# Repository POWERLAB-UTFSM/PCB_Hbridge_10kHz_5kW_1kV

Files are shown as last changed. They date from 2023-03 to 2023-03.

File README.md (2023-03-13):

# Proyecto PCB Hbridge

## Descripción

Repositorio con archivos necesarios para visualizar el esquematico y PCB del circuito Hbridge

## Requisitos

### Software

* KiCad, para diseño de esquemático y conversión a placa de circuito impreso
* Git, para control de versiones y manejo de repositorios.

## Contenido de carpetas:

* [PCB_Hbridge](PCB_Hbridge): Carpeta con archivos relacionados al esquematico y 
    * [BOM](PCB_Hbridge/BOM): Carpeta con lista detallada de todos los componentes electrónicos necesarios para construir un circuito impreso (PCB) obtenida directamente desde el software.
    * [GERBER](PCB_Hbridge/GERBER): Carpeta con archivos necesarios para la fabricación de la PCB.

* [BOM_v1](BOM_v1): Lista detallada con los componentes y su precio, dando un estimado del presupuesto necesario para su fabricación.

* [Documento_de_diseno](Documento_de_diseno): Documento que respalda el diseño y desarrollo del circuito implementado en la PCB

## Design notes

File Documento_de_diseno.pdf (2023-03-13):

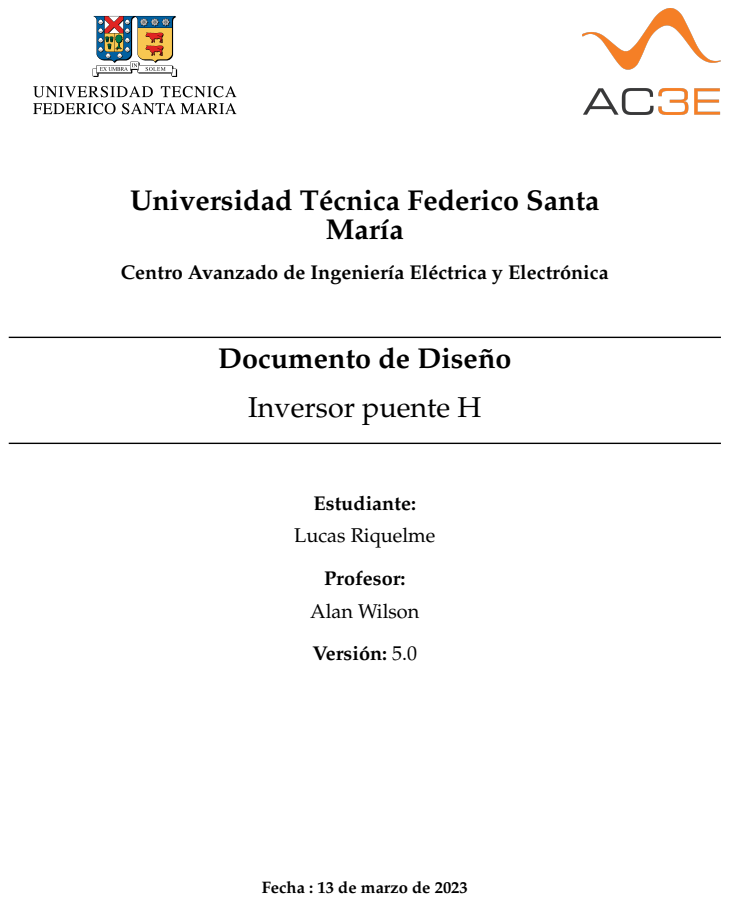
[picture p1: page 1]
María; Estudiante:; Lucas Riquelme; Profesor:; Alan Wilson; Versión: 5.0

Universidad Técnica Federico Santa

Centro Avanzado de Ingeniería Eléctrica y Electrónica

Documento de Dise ño
Inversor puente H

Fecha : 13 de marzo de 2023

## Prefacio

Alcance del
documento

Establece los requisitos funcionales que debe cumplir el diseno del Inversor ˜ Puente H. Describe los siguientes aspectos del sistema: requisitos funciona-
| les, arquitectura del sistema a disenar, caracter ˜ | ísticas funcionales de cada
componente, descripcion de cada m ´ | odulo, incluyendo sus casos de prueba. ´
Autor | Lucas Riquelme
Lectores | Este documento esta dirigido principalmente al supervisor de pr ´ | actica ´

## Historia del documento

Versión | Fecha | Descripción del cambio | Autor
1.0 | 05/01/2023 | Primer documento LATEX | Lucas Riquelme
2.0 | 17/01/2023 | Se agregan secciones principales | Lucas Riquelme
3.0 | 30/01/2023 | Se agrega el desarrollo del modulo in- ´ versor y filtro | Lucas Riquelme
4.0 | 08/02/2023 | Se agrega el desarrollo del modulo ´ circuito de medicion´ | Lucas Riquelme
5.0 | 27/02/2023 | Se complementa el desarrollo del cir-cuito de medicion y se agrega simula- ´ cion con rectificador en la secci ´ on de ´ filtro de salida | Lucas Riquelme
Documento de disenõ | 1

## Índice

1. Descripción y requisitos del sistema | 3
1.1. Proposito | ´ | 3
1.2. Requisitos funcionales | | 3
1.3. Alcances | | 3
2. Arquitectura del sistema | 4
2.1. Diagrama de bloques | | 4
2.2. Enumeracion de m ´ | odulos | ´ | 4
3. Descripción de los módulos | 5
3.1. Modulo Inversor monof ´ | asico | ´ | 5
3.1.1. Definicion | ´ | 5
3.1.2. Diagrama del modulo | ´ | 5
3.1.3. Diseno del m ˜ | odulo | ´ | 5
3.1.4. Estrategia de prueba del modulo | ´ | 8
3.2. Modulo Filtro paso bajos | ´ | 9
3.2.1. Definicion | ´ | 9
3.2.2. Diagrama del modulo | ´ | 9
3.2.3. Diseno del m ˜ | odulo | ´ | 9
3.2.4. Estrategia de prueba del modulo | ´ | 13
3.3. Modulo Circuito de medici ´ | on | ´ | 14
3.3.1. Definicion | ´ | 14
3.3.2. Diagrama del modulo | ´ | 14
3.3.3. Diseno del m ˜ | odulo | ´ | 14
3.3.4. Estrategia de prueba del modulo | ´ | 17
3.4. Lista de componentes (BOM) | 18

## Índice de figuras

1. | Diagrama de bloques del sistema | | 4
2. | Diagrama de circuito del modulo Inversor monof ´ | asico | ´ | 5
3. | Esquematico del inversor puente H y modulaci ´ | on PWM unipolar | ´ | 6
4. | Resultados obtenidos en el modulo inversor monof ´ | asico | ´ | 7
5. | Filtro LC | | 9
6. | Esquematico del inversor puente H y filtro LC | ´ | 10
7. | Resultados obtenidos en el modulo filtro de salida | ´ | 11
8. | Esquematico del inversor m ´ | as filtro, considerando rectificador | ´ | 12
9. Resultados obtenidos utilizando el rectificador de entrada | 12
10. Diagrama de bloques del modulo circuito de medici ´ | on | ´ | 14
11. Circuito de sensor de voltaje | 15
12. Sensor de corriente integrado MLX91221 | 15
13. Convertidor DC/DC PDSE2-S24-S5-M | 16

## Índice de cuadros

1. | Modulos del sistema | ´ | 4
2. | Parametros base del inversor puente H a modelar | ´ | 7

## 1. Descripción y requisitos del sistema

Esta seccion explica el prop ´ | osito y funcionamiento general del sistema a dise ´ | nar, junto con ˜
describir los requisitos funcionales y alcances del sistema.

### 1.1. Propósito

El sistema corresponde a un convertidor DC/AC, el cual debe ser capaz de convertir un voltaje
continuo a una tension alterna de alta frecuencia. Adem ´ | as, de entregar se ´ | nales acondicionadas ˜
para observar las mediciones en la entrada y salida del sistema.

### 1.2. Requisitos funcionales

Los requisitos funcionales definen el comportamiento del sistema. En otras palabras, estos requisitos mínimos describen que es lo que debe hacer el sistema.

RF1 La tension continua de entrada de 1kV debe ser convertida en un voltaje conmutado con ´ frecuencia fundamental de 10kHz, el cual debe ser filtrado para obtener un voltaje alterno sin armonicos de alta frecuencia. ´

RF2 El sistema debe entregar una potencia de hasta 5kW.

RF3 El sistema es capaz de medir voltajes DC y AC de hasta 1kV.

RF4 Las senales an ˜ | alogas de las mediciones generadas por el circuito est ´ | an adaptadas para ran- ´
gos de ±5V para ser visualizadas en un osciloscopio.

### 1.3. Alcances

La entrada del sistema corresponde a un DC-link de 1kV obtenido a partir de un modulo ´ rectificador.

La salida del sistema debe estar conectada a un transformador, por tanto el voltaje alterno a la salida del sistema debe tener valor medio cero.

## 2. Arquitectura del sistema

Aquí se presenta la arquitectura que se empleara para desarrollar el Inversor puente H. ´

### 2.1. Diagrama de bloques

La siguiente figura muestra los modulos internos y externos del sistema, y sus principales ´ interacciones.

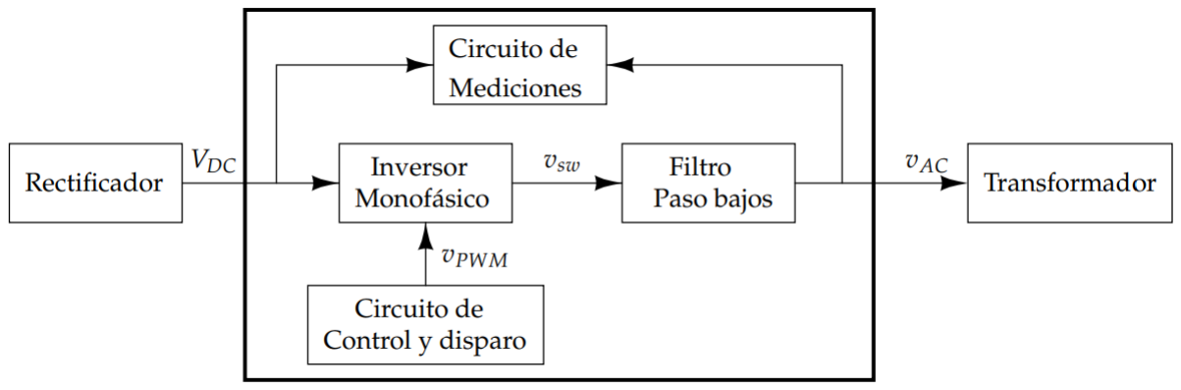
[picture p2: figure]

Figura 1: Diagrama de bloques del sistema

### 2.2. Enumeración de módulos

La Tabla 1 muestra los bloques de la Figura 1. Por cada modulo se entrega un breve p ´ | arrafo ´
descriptivo de su proposito. ´
Modulo ´ | Proposito ´
Inversor monofasico ´ | Convertir el voltaje continuo de entrada en una tension alterna ´
Filtro paso bajos | Filtrar los armonicos de alta frecuencia de una se ´ nal alterna ˜
Circuito de medicio-nes | Adapta los voltajes de entrada y salida
Circuito de control y disparo | Genera los pulsos de disparo que controlan al inversor

Cuadro 1: Modulos del sistema. ´

## 3. Descripción de los módulos

### 3.1. Módulo Inversor monofásico

### 3.1.1. Definición

Propósito: Convertir un voltaje dc de 1kV a una tension alterna de frecuencia 10kHz ´

### 3.1.2. Diagrama del módulo

La figura 2 muestra el diagrama del modulo Inversor monof ´ | asico. ´

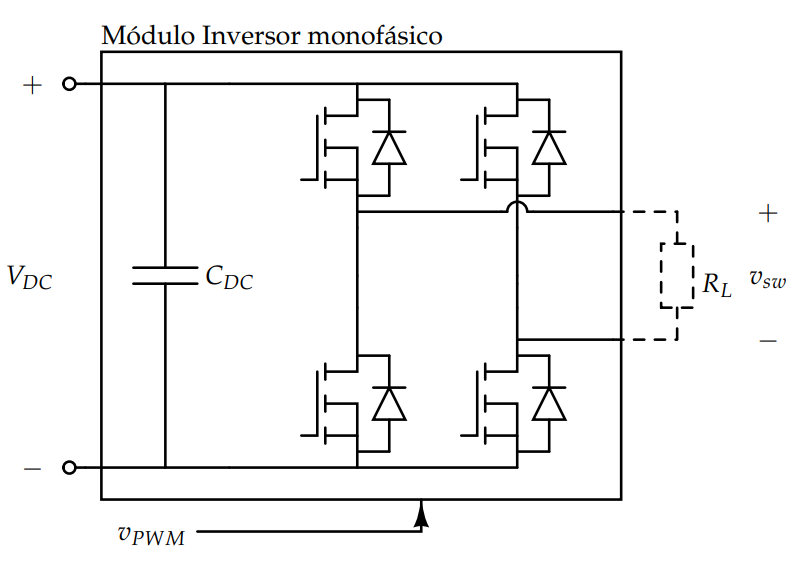
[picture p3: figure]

Figura 2: Diagrama de circuito del modulo Inversor monof ´ | asico. ´

### 3.1.3. Dise ño del módulo

Lo primero a considerar es el tipo de modulacion a utilizar, dado a que se necesita generar un ´ voltaje alterno con valor medio cero, se utiliza la modulacion PWM unipolar para generar una ´
tension a la salida de tres niveles. Hay que considerar que, al utilizar este tipo de modulaci ´ | on´
se obtendra una duplicaci ´ | on aparente de la frecuencia de conmutaci ´ | on a la salida, con lo que se ´
consigue alejar los armonicos de ´ | mf a 2mf ± 1.
Por otro lado, se escoge un índice de modulacion par ( ´ | mf = 10) dado a que permite eliminar los
armonicos pares que se generen, con este valor y considerando que la frecuencia de la fundamental ´ es f1 = 10kHz, es posible obtener el valor de la frecuencia de la portadora a utilizar,

fc = mf

f1 = 100kHz | (1)

Por otro lado, se sabe que el circuito debe entregar una potencia de hasta Po = 5kW a una tension´ Vdc = 1kV, es decir, la carga conectada debe ser una resistencia de,

RL =

(VDC)

2
P
= 200Ω | (2)

y por tanto, la corriente en la carga y en el semiconductor es,

IL =

VDC
RL
= 5A | (3)

Para el semiconductor, se utiliza el MOSFET de carburo de silicio dado a que generalmente operan a altas frecuencias y velocidad de conmutacion, y soportan una mayor temperatura de ´ juntura. Por otro lado, hay que tener en cuenta que estos deben ser capaces de operar a una frecuencia de 100kHz, soportar un voltaje de 1kV y una corriente de IL = 5A. Dado a que se debe tener un margen de seguridad en caso de algun peak de corriente o voltaje, al momento de escoger ´ un MOSFET se establecen los siguientes criterios,

VDSS ≥ 1,2 · VDC = 1200V | (4)
ID ≥ 2 · IL = 10A | (5)
Finalmente, para el diseno del condensador del DC-link, se considerar ˜ | a un criterio basado en ´
el rizado del voltaje DC, cuya formula esta dada por,

CDC =

Ig
8 fsw∆V

(6)

Donde Ig es la corriente peak y fsw la frecuencia de conmutacion, por otro lado, ´

∆V = r · Vo | (7)

Considerando un rizado del 5 % y un valor medio de 1000V, se obtiene que el valor de la capacitancia del DC-link debe ser de 0.12µF.
Se escoge un SiC-MOSFET SCT4062KRHR de Rohm Semiconductor, el cual cumple con las características anteriormente nombradas. Utilizando su modelo en PLECS se simula el convertidor para observar las perdidas totales en el semiconductor, su temperatura de juntura, voltaje, ´ corriente y potencia en la carga.

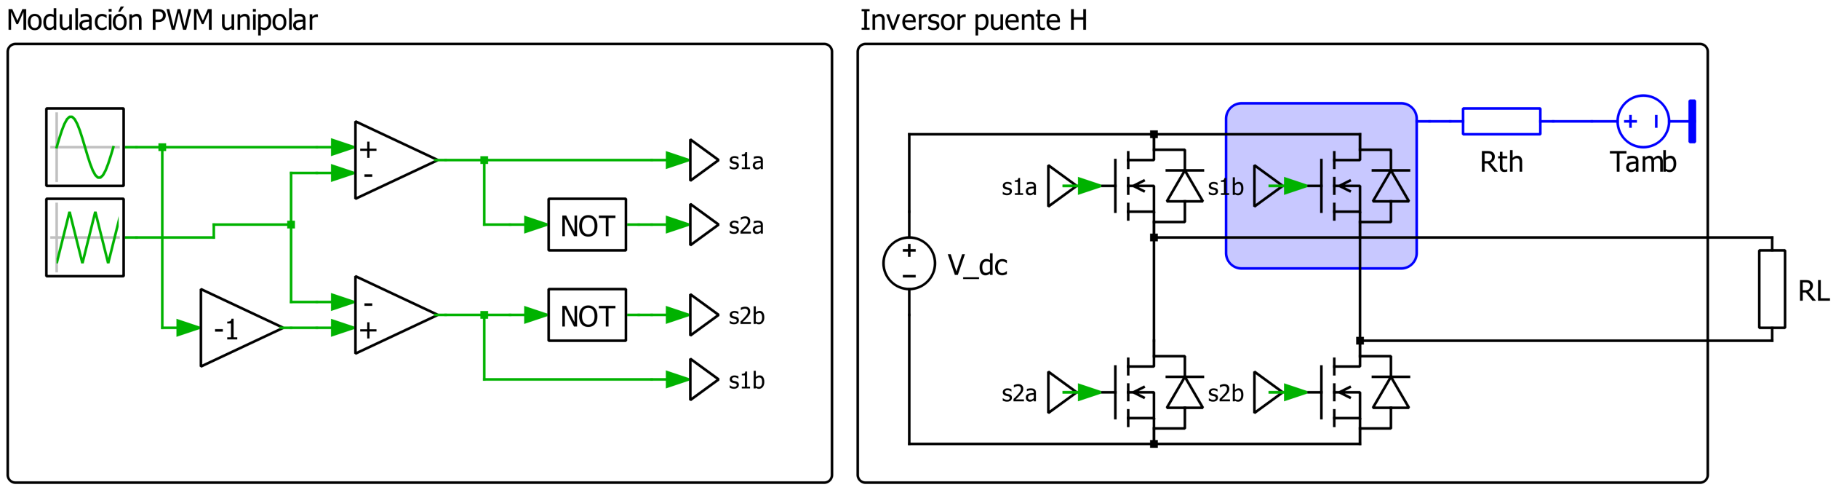
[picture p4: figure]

Figura 3: Esquematico del inversor puente H y modulaci ´ | on PWM unipolar. ´
Cabe mencionar que para la simulacion, se utilizaron los siguientes par ´ | ametros mostrados en ´
la tabla 2,

Cuadro 2: Parametros base del inversor puente H a modelar. ´

Descripción | Parámetro | Valor
Voltaje en la fuente DC | VDC | 1000 V
Resistencia en la carga | RL | 200 Ω
Frecuencia fundamental | f1 | 10 kHz
Frecuencia de portadora | fc | 100 kHz
Índice de modulacion (amplitud) ´ | m | 1
Resistencia termica del disipador ´ | Rthc,ca | 7 C ◦/W
Temperatura ambiente | Tamb | 25 C ◦

Obteniendo los siguientes resultados de simulacion, ´

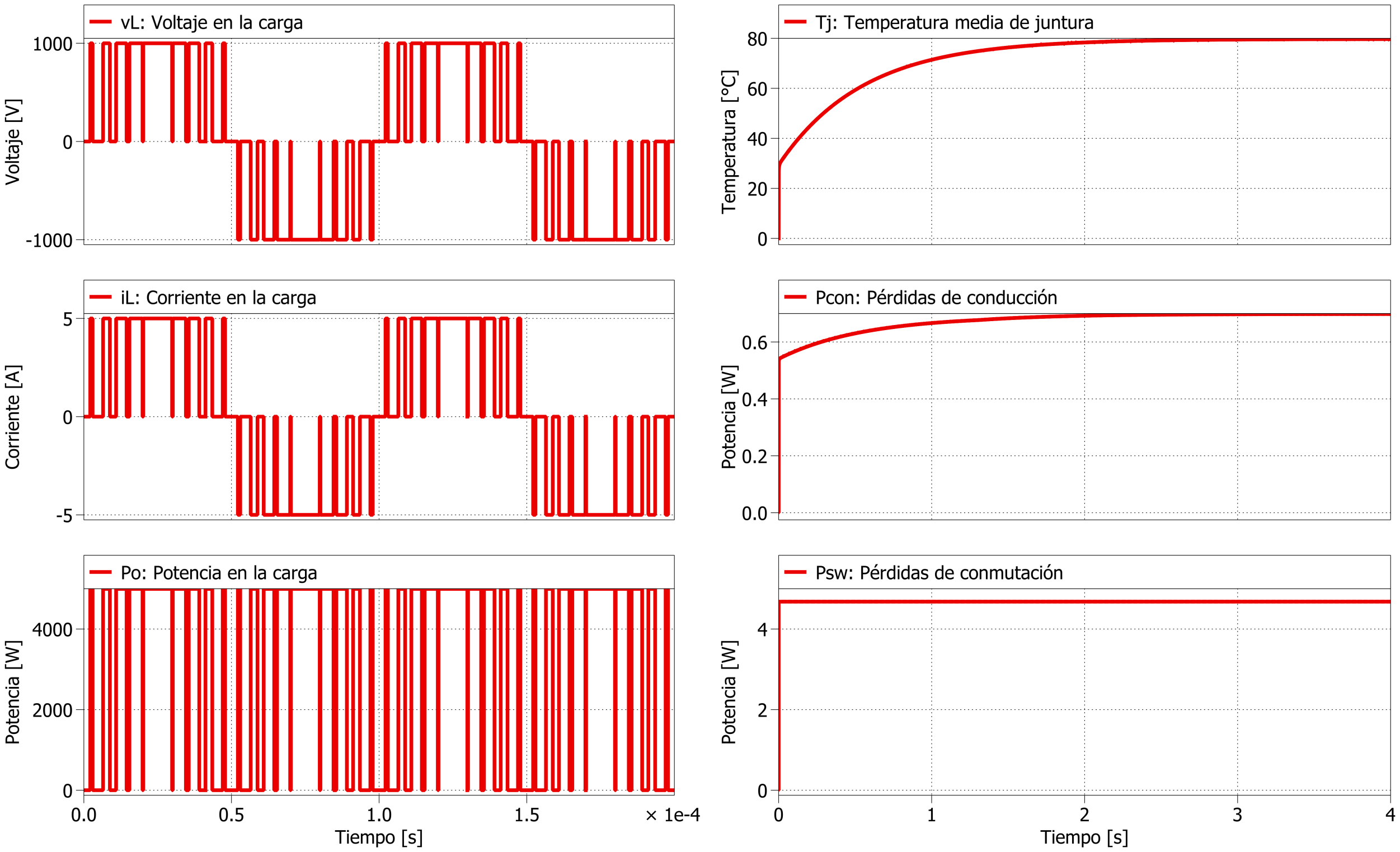
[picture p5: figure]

(a) Voltaje, corriente y potencia en la carga. | (b) Temperatura y perdidas en el MOSFET. ´
Figura 4: Resultados obtenidos en el modulo inversor monof ´ | asico. ´

En la figura 4.b se observa que el MOSFET alcanza una temperatura media de juntura de 79.7 C ◦
, la cual esta dentro de lo especificado en el datasheet. Por otro lado, se observa que las
perdidas de conducci ´ | on llega a 0.6981W y las p ´ | erdidas de conmutaci ´ | on llega a 4.6785W, dando ´
unas perdidas totales de 5.3766W. ´

Cabe mencionar que, la resistencia termica que se considero para el “heat sink” fue obtenida ´ a partir de un disipador encontrado en el mercado, el cual cumple con las dimensiones del SiC-MOSFET (TO-247-4L).

### 3.1.4. Estrategia de prueba del módulo

Para la prueba del modulo se utilizara una fuente de tensi ´ | on DC que sea capaz de suministrar ´
1000V a la entrada del inversor puente H, ademas de utilizar un microcontrolador para generar ´ los pulsos de disparo que controlaran al puente H. Para finalmente medir la senal de salida entes ˜ del filtro para observar su voltaje y frecuencia.

### 3.2. Módulo Filtro paso bajos

### 3.2.1. Definición

Propósito: Filtrar las componentes armonicas de alta frecuencia del voltaje de salida del con- ´ vertidor.

### 3.2.2. Diagrama del módulo

La figura 5 muestra el diagrama del modulo Filtro de salida. ´

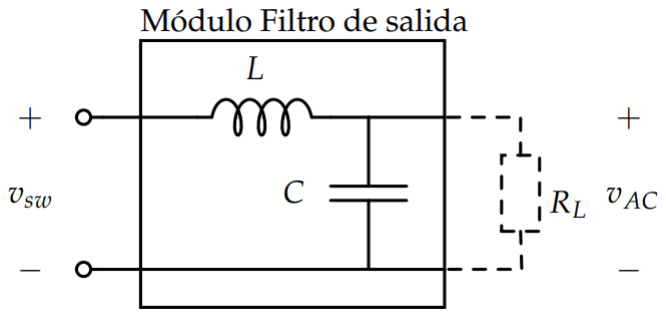
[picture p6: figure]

Figura 5: Filtro LC.

### 3.2.3. Dise ño del módulo

Se escoge un filtro del tipo LC a la salida debido a que permite eliminar los armonicos de alta ´ frecuencia y a su facilidad de diseno. ˜
Analizando el circuito en utilizando la transformada de Laplace, se obtiene la siguiente funcion´ de transferencia,
Vf(s)
Vs f(s)

=

1
LC
s

2 + 1

RC s + 1
LC

(8)

Por definicion, las ecuaciones para el factor de amortiguaci ´ | on y la frecuencia de corte del filtro LC ´
son:

ωo =

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
(10)

Despejando L y C en funcion de los valores conocidos, ´

C =

1
2ξRωo

(11)

L =

2ξR

ωo

(12)

Donde R = 200Ω y se escoge ξ = 1/√
2. Para la frecuencia de corte se escoge una decada menos ´ que la frecuencia del voltaje de salida, es decir,

fo =

2 fc
10 = 20kHz | (13)

Reemplazando estos valores en las ecuaciones (11) y (12), se obtiene,

C = 2,8nF | (14)
L = 2,3mH | (15)

Si bien estos no son valores comerciales, se pueden obtener valores cercanos con condensadores en paralelo o inductores en serie. Ademas hay que considerar que el inductor debe ser capaz de ´ soportar corrientes mayores a 5.5A y el condensador voltajes mayores a 1200V, de forma de tener un margen de seguridad. En el mercado se encontraron valores cercanos, para el condensador un valor de 10000pF y para el inductor un valor de 500µH. Por lo tanto, utilizando dos inductores en serie y 3 condensadores en paralelo se obtienen resultados optimos en el voltaje alterno de salida. ´
A continuacion se muestra el esquema utilizado para la simulaci ´ | on, donde se utilizo un valor ´
de capacitancia C = 30000pF y una inductancia de 1mH para el filtro LC, ademas de conectar la ´ carga a la salida de 200Ω,

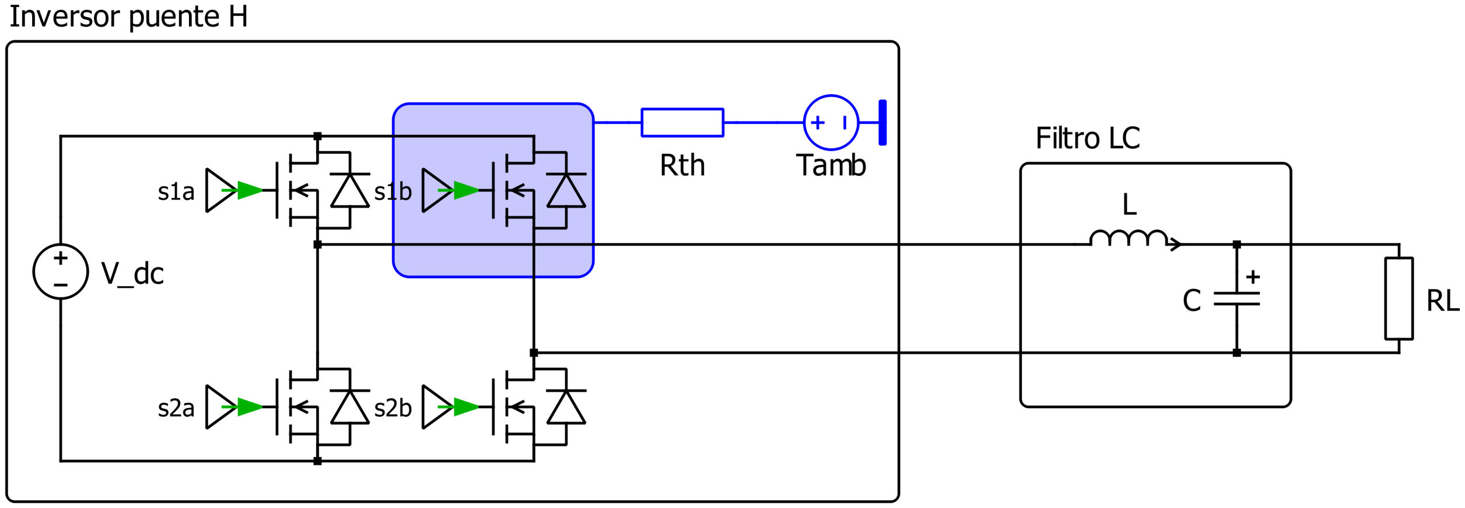
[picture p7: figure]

Figura 6: Esquematico del inversor puente H y filtro LC. ´

Al simular se obtuvieron los siguientes resultados mostrados en la figura 7 donde se destaca que,

En la figura 7.a y 7.b se observa que se obtiene un voltaje alterno sinusoidal a la salida, donde se eliminan todas las armonicas de lata frecuencia. ´

Por otro lado, se observa que al utilizar el filtro de salida la temperatura media de juntura disminuye a 61.5344 C ◦
. Ademas, las p ´ | erdidas totales del semiconductor disminuyen a ´
3.5886W.

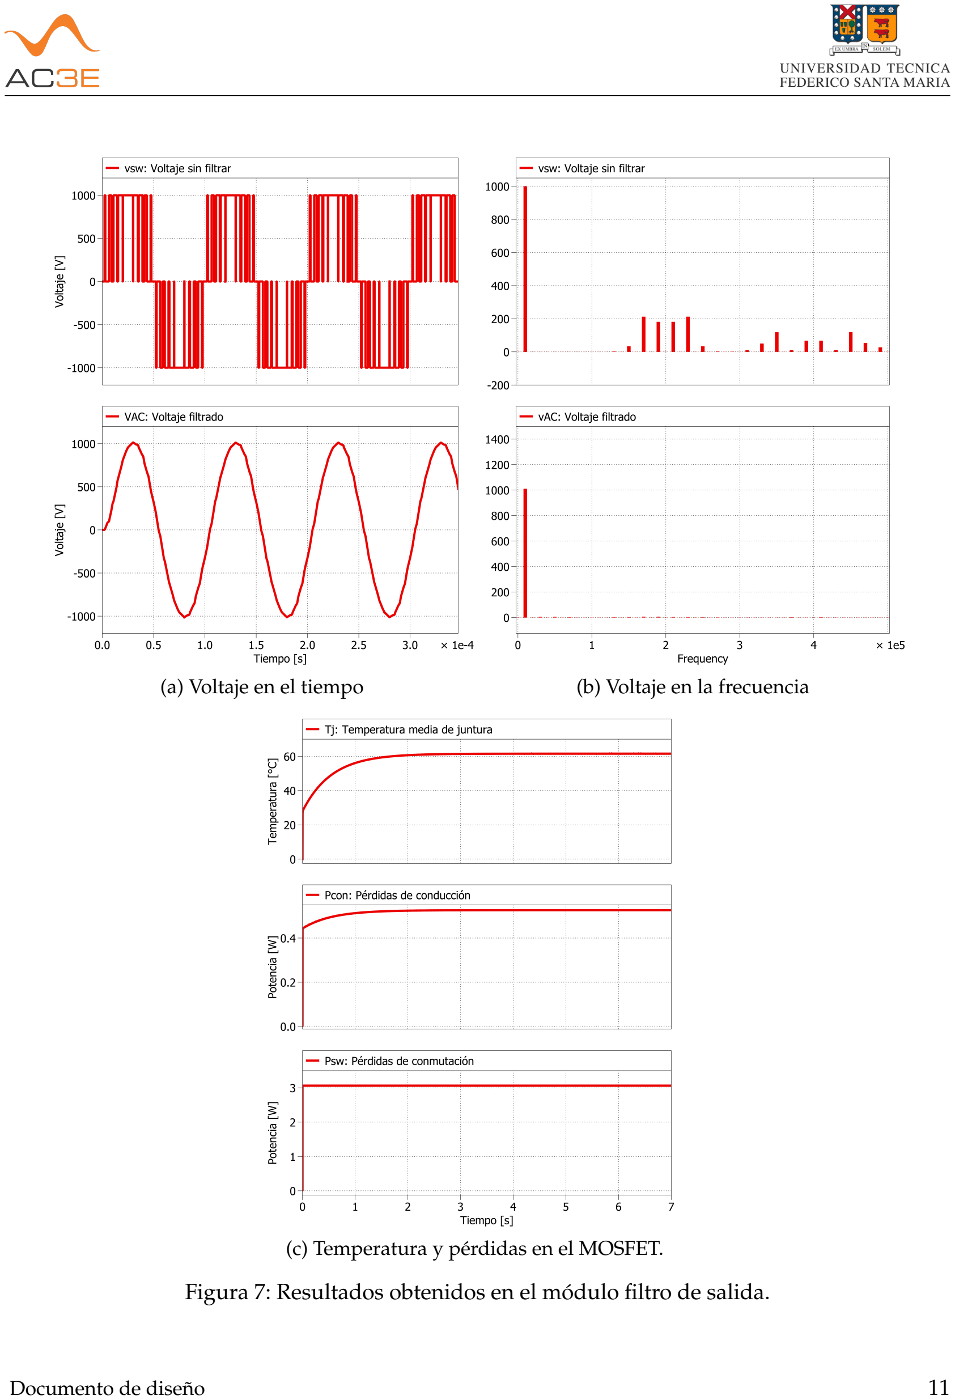
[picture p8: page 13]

(a) Voltaje en el tiempo | (b) Voltaje en la frecuencia
(c) Temperatura y perdidas en el MOSFET. ´

Figura 7: Resultados obtenidos en el modulo filtro de salida. ´

Para finalizar, se simulara el inversor m ´ | as filtro, considerando que en la entrada tiene un rec- ´
tificador trifasico puente, considerando un voltaje de entrada de 545V, de forma de obtener apro- ´ ximadamente un voltaje medio a la del rectificador de 1000V, tal como se muestra en la siguiente expresion, ´

Vo =

3

√
3Vi

π

= 901V | (16)
A continuacion se muestra el esquem ´ | atico utilizado en la simulaci ´ | on, ´

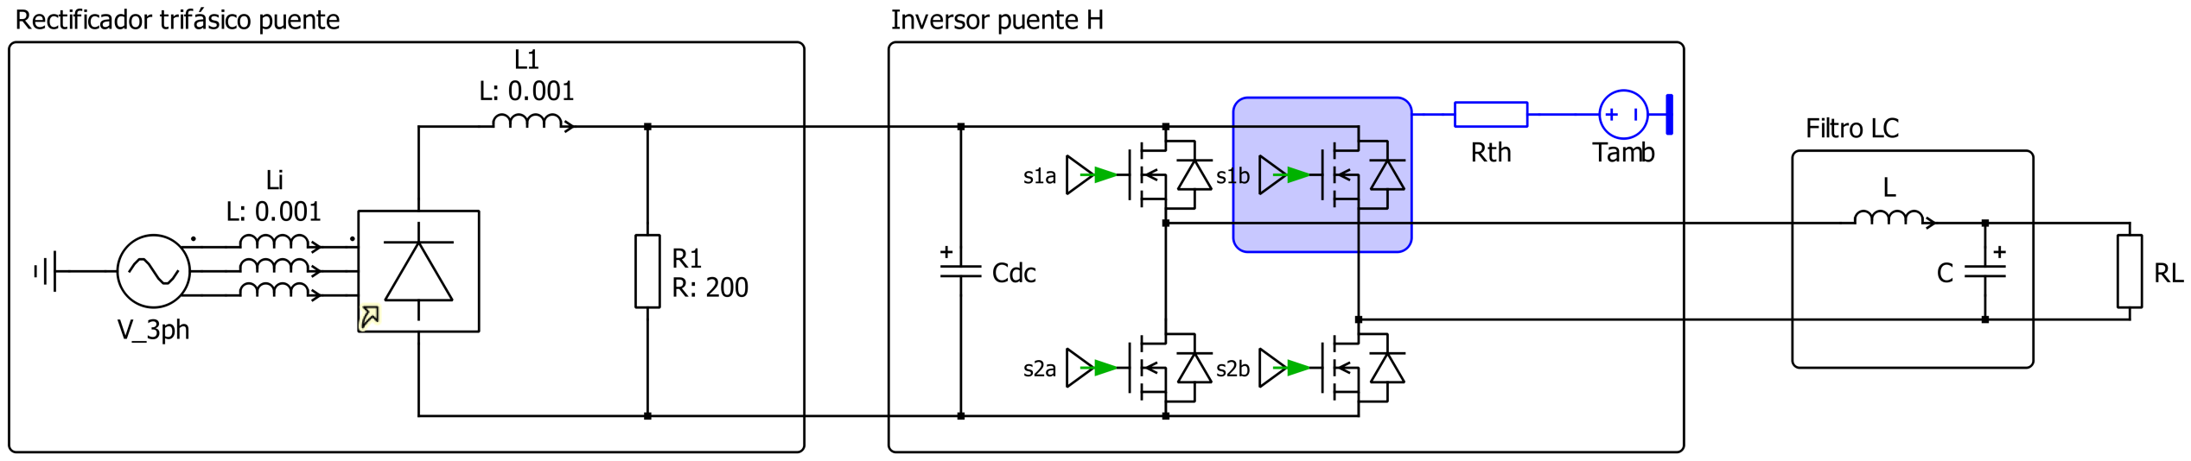
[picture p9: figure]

Figura 8: Esquematico del inversor m ´ | as filtro, considerando rectificador. ´

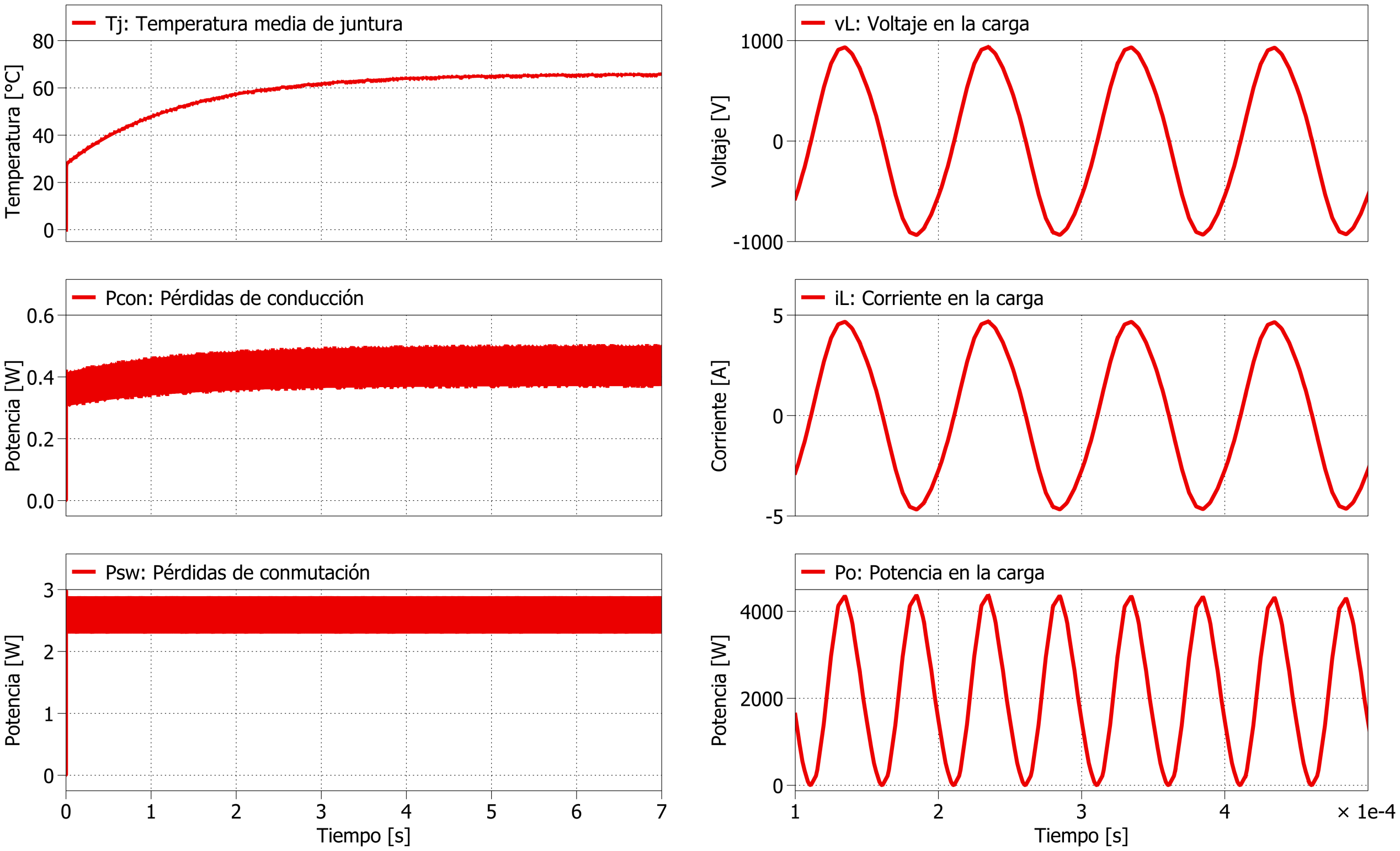
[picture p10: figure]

(a) Temperatura y perdidas en el MOSFET. ´ | (b) Voltaje, corriente y potencia en la carga.

Figura 9: Resultados obtenidos utilizando el rectificador de entrada.

En la figura 9.a se observa que la temperatura de juntura llega hasta los 65 C ◦ y que las perdidas totales llegan a 3.3568W. ´

En la figura 9.b se observa que el voltaje, corriente y potencia no varía en comparacion a no ´ utilizar el rectificador, alcanzando valores similares.

### 3.2.4. Estrategia de prueba del módulo

Para probar el correcto funcionamiento del modulo, se proceder ´ | a de la misma forma que en el ´
caso anterior, con la diferencia que esta vez se medira el voltaje obtenido a la salida del filtro, el ´
cual debera tener unos valores similares a los obtenidos mediante simulaci ´ | on. ´

### 3.3. Módulo Circuito de medición

### 3.3.1. Definición

Propósito: Adaptar las senales de voltaje y corriente de entrada y salida ˜

### 3.3.2. Diagrama del módulo

La figura 10 muestra el diagrama del modulo Circuito de medici ´ | on. ´

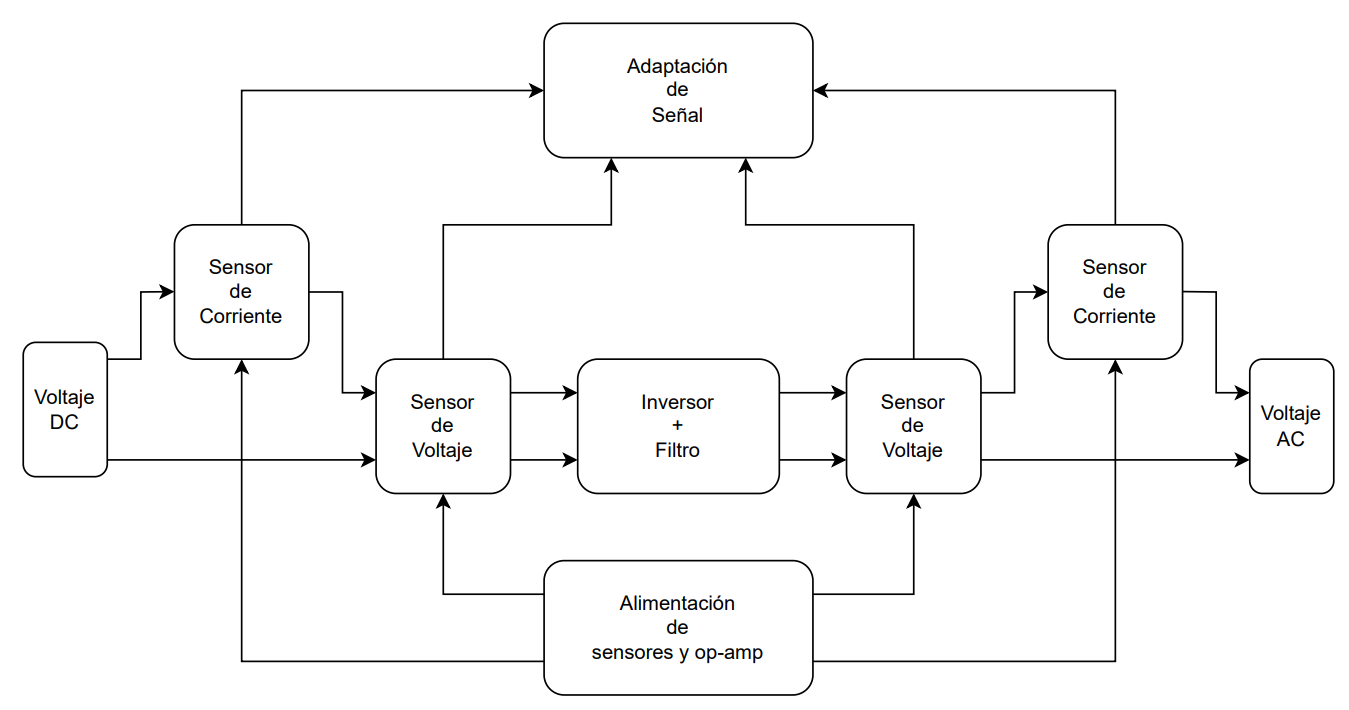
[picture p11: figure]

Figura 10: Diagrama de bloques del modulo circuito de medici ´ | on. ´

### 3.3.3. Dise ño del módulo

A continuacion de muestran los detalles generales por bloque del diagrama de la figura 10. ´

Sensor de voltaje: Corresponde a un sensor capaz de medir tensiones de hasta 1kV, donde
la senal de entrada es el voltaje ˜ | ±VDC (sensor de entrada) y ±VAC (sensor de salida). Las
senales de salida van a una etapa de adaptaci ˜ | on de se ´ | nal. ˜
En esta etapa se utilizo un amplificador de aislamiento, dado a que permite justamente aislar
la medicion de voltaje del circuito inversor, adem ´ | as generalmente estos tienen un alto ancho ´
de banda. Se escogio el modelo ACPL-790B-300E dado a su precio, su alto ancho de banda ´ (200 kHz) y la salida es adaptable tanto para el rango entre 0-3.3V y ±5V.
Este amplificador tiene como rango de entrada ±200mV, por lo que se utiliza un arreglo de resistencias para adaptar la senal de 1kV al rango deseado, tal como se muestra en el ˜ siguiente esquema,

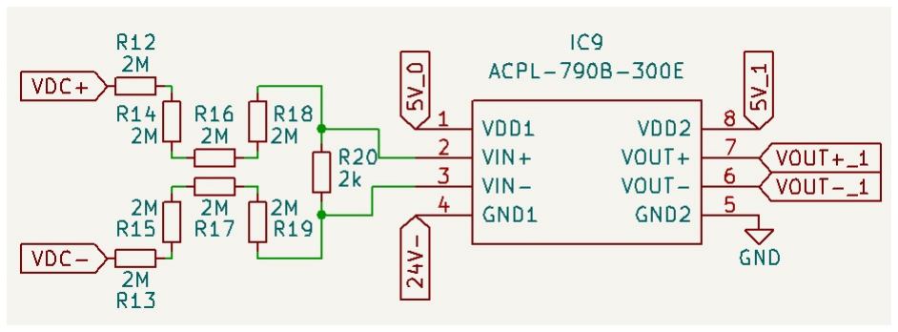
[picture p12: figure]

Figura 11: Circuito de sensor de voltaje.

Este arreglo ajusta la senal de 1000kV a 125mV, por datasheet, se desprende que este ampli- ˜ ficador tiene una ganancia de 8, por lo que el voltaje a la salida es de 1V, y este voltaje luego
pasara a una etapa de adaptaci ´ | on de se ´ | nal. Adem ˜ | as, cabe mencionar que para el funciona- ´
miento del amplificador se debe utilizar una alimentacion de 5V. ´

Sensor de corriente: Corresponde a un sensor capaz de medir corrientes en un rango de hasta 25A, cuyas senales de entrada son la corriente que recibe una carga conectada en serie ˜ a la entrada del DC-link (sensor de entrada) y salida del filtro LC (sensor de salida). Las
senales de salida van a una etapa de adaptaci ˜ | on de se ´ | nal. ˜

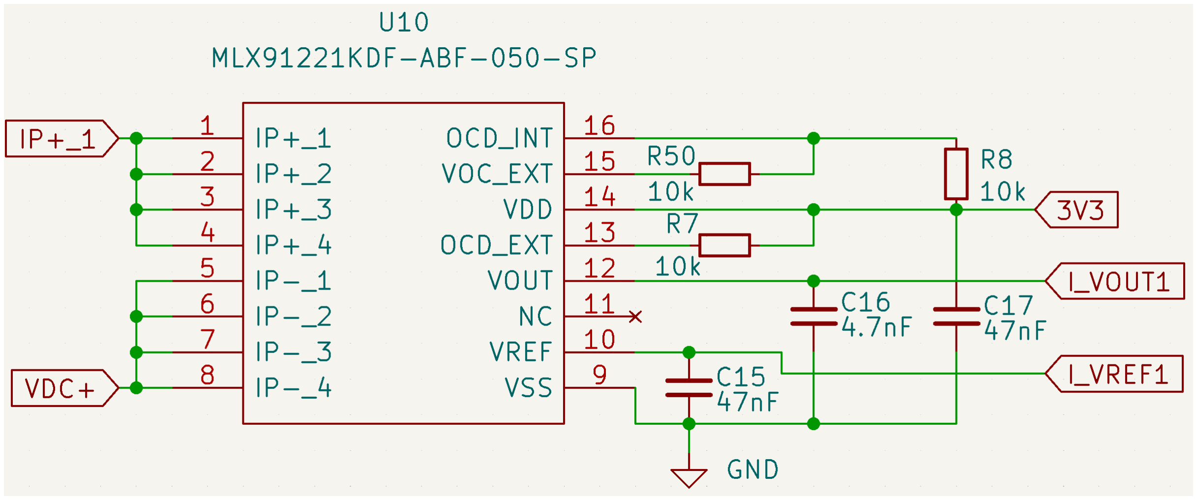
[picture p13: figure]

Figura 12: Sensor de corriente integrado MLX91221.

Cabe mencionar, que la configuracion utilizada en la figura 12, es la recomendada por el ´ datasheet (https://www.mouser.cl/datasheet/2/734/MLX91221_Datasheet_Melexis-2885853.pdf) y esta va conectada en serie a la entrada y salida del inversor mas filtro, donde ´ el voltaje IVOUT1 y IVREF1 corresponden a un voltaje proporcional a la corriente medida, los cuales tienen una amplitud de 1.65V.

Alimentación de sensores y op-amp: Corresponden a un conjunto de convertidores DC-DC aislado capaz de trasformar la tension de entrada de 24V a 5V (para alimentar a los sensores) ´ y ±12V (para alimentar los acondicionadores de senal). ˜
Considerando que se tendra una fuente de alimentaci ´ | on de 24V, se utilizaran tres modelos ´
de convertidores DC/DC aislados,

- Convertidor DC/DC PDSE2-S24-S5-M (24V a 5V): Para alimentar el sensor de voltaje.

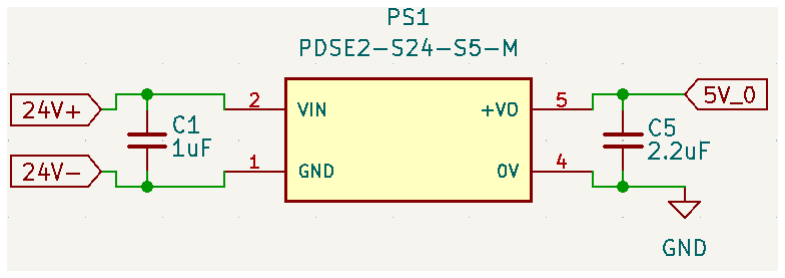
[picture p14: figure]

Figura 13: Convertidor DC/DC PDSE2-S24-S5-M.

- Convertidor DC/DC AP7366-W5-7 (5V a 3.3V / 1.65V): Para alimentar el sensor de corriente y el otro para adaptar la senal. ˜

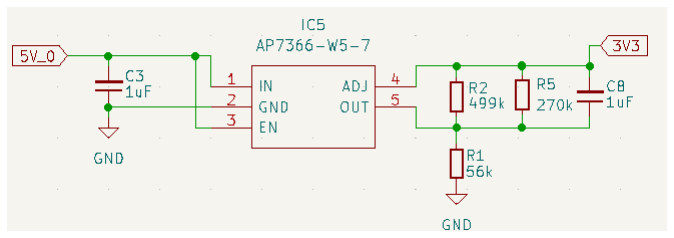
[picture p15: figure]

Figura 14: Convertidor DC/DC AP7366-W5-7.

En este caso, se utilizo un arreglo de resistencia recomendado por el datasheet, cuya formula esta dada por (considerando la figura 14):

VOUT = 0,8
1 +

R2//R5
R1
(17)
- Convertidor DC/DC PEM2-S24-D12-S (24V a ±12V): Para alimentar los amplificadores operacionales utilizados para adaptar las senales. ˜

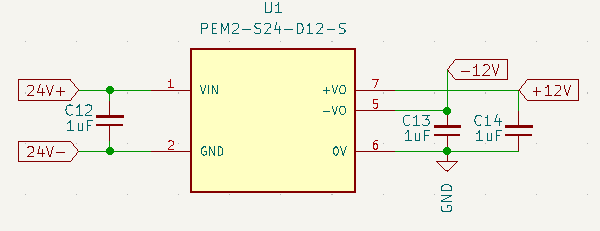
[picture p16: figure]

Figura 15: Convertidor DC/DC PEM2-S24-D12-S.

Cabe mencionar, que todos los condensadores utilizados en esta etapa fueron obtenidos a partir de los recomendados por la hoja de datos de cada modelo.

Adaptación de se ñal: Corresponde a un conjunto de amplificadores operacionales que adap-
tan las senales recibidas por los sensores a un rango entre 0-3.3V ˜ | ó ±5V.

### 3.3.4. Estrategia de prueba del módulo

Sensor de voltaje: Se corrobora que las tensiones esperadas en el divisor resistivo esten den- ´
tro del rango observado en simulacion (por ejemplo, LTspice) y el dise ´ | nado te ˜ | oricamente, ´
para esto se hace uso de un tester digital para medir los voltajes DC de forma experimental. Luego, para ratificar el correcto funcionamiento del sensor, se utiliza una generador de funciones para designar una senal de entrada al sensor que posea un rango entre 0 y 2V, con ˜ el fin de observar a la salida del mismo una tension lineal y proporcional al cambio en la ´ entrada, ya que la principal característica del sensor es su alta linealidad.

Sensor de corriente: Se corrobora conectando una carga variable en serie junto a una fuente de voltaje, de forma de variar la corriente y verificar, ya sea con un multímetro o un osciloscopio, que los valores de salida entregados sean proporcionales a la corriente medida.

Conversión de voltaje: Se corrobora que los convertidores DC-DC adquiridos esten operan- ´ do correctamente, utilizando un tester digital para medir y verificar que la tension a la salida ´ de los convertidores sea la correcta.

Acondicionamiento de voltaje: Se conecta un generador de funciones a la entrada con amplitudes similares a las generadas en la etapa anterior, para verificar mediante un osciloscopio y/o microcontrolador que el voltaje se adapte a los valores deseados.

### 3.4. Lista de componentes (BOM)

A continuacion se adjunta la lista de materiales y su ubicaci ´ | on, en el siguiente link. (https://docs.google.com/spreadsheets/d/1sQ2gJbRkboxfMOcj0LNilNcOAhUPTTo0/edit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) ´

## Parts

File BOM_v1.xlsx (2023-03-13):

Quantity | Manufacturer Name | Manufacturer Part Number | Mouser Part Number | Description / Value | Unit Price (CLP) | Total (CLP)
4 | ROHM Semiconductor | SCT3105KRC14 | 755-SCT3105KRC14 (https://www.mouser.cl/ProductDetail/ROHM-Semiconductor/SCT3105KRC14?qs=XeJtXLiO41TNpuiX4HR%252Bvw%3D%3D) | SICFET N-CH 1200V 24A TO247-4L | $23766 | $95064
3 | TDK Corporation | S103M69Z5UP63K7R | 594-S103M69Z5UP63K7R (https://www.mouser.cl/ProductDetail/Vishay-BC-Components/S103M69Z5UP63K7R?qs=kWu6FN6bAPw%2FsZemloGzLw%3D%3D) | Ceramic Capacitor 0.01uF | $1989 | $5967
1 | Vishay | TJ92UEB222L | 70-TJ92UEB222L (https://www.mouser.cl/ProductDetail/Vishay/TJ92UEB222L?qs=xZ%2FP%252Ba9zWqaX%2FODTtGMuhA%3D%3D) | Toroidal Inductor 2.2mH | $20859 | $20859
4 | Ohmite | WA-T247-101E | 588-WA-T247-101E (https://www.mouser.cl/ProductDetail/Ohmite/WA-T247-101E?qs=TVIBDWOgMcWKH4aeLeQEMg%3D%3D) | Heat Sink 7°C/W | $3311 | $13244
2 | CUI Inc | PDSE2-S24-S5-M | 490-PDSE2-S24-S5-M (https://www.mouser.cl/ProductDetail/CUI-Inc/PDSE2-S24-S5-M?qs=7D1LtPJG0i1g0MAknAJyHw%3D%3D) | DC/DC Converter 24V to 5V | $6622 | $13244
9 | YAGEO | AC0805KFX7R9BB105 | 603-AC805KFX7R9BB105 (https://www.mouser.cl/ProductDetail/YAGEO/AC0805KFX7R9BB105?qs=A6eO%252BMLsxmSrnyA4182Guw%3D%3D) | SMD Capacitor 1uF | $535 | $4815
2 | Murata Electronics | GCM31CR71H225KA55K | 81-GCM31CR71H225KA5K (https://www.mouser.cl/ProductDetail/Murata-Electronics/GCM31CR71H225KA55K?qs=Er06SXQpt%252B4Wl7IFhiz7sg%3D%3D) | SMD Capacitor 2.2uF | $393 | $786
2 | Diodes Incorporated | AP7366-W5-7 | AP7366-W5-7DITR-ND (https://www.digikey.com/en/products/detail/diodes-incorporated/AP7366-W5-7/9867323) | Linear Voltage Regulator 5V to 3V3/1V65 | $481 | $962 | (Digi-key)
2 | Bourns | CR0805-FX-5602ELF | 652-CR0805FX-5602ELF (https://www.mouser.cl/ProductDetail/Bourns/CR0805-FX-5602ELF) | SMD Resistor 56k | $109 | $218
10 | Vishay / Dale | CRCW0805120KFKEAC | 71-CRCW0805120KFKEAC (https://www.mouser.cl/ProductDetail/Vishay-Dale/CRCW0805120KFKEAC) | SMD Resistor 120k | $131 | $1310
1 | Vishay / Dale | CRCW0805270KFKEAC | 71-CRCW0805270KFKEAC (https://www.mouser.cl/ProductDetail/Vishay-Dale/CRCW0805270KFKEAC) | SMD Resistor 270k | $131 | $131
11 | Bourns | CR0805-FX-4993ELF | 652-CR0805FX-4993ELF (https://www.mouser.cl/ProductDetail/Bourns/CR0805-FX-4993ELF) | SMD Resistor 499k | $109 | $1199
1 | CUI Inc | PEM2-S24-D12-S | 490-PEM2-S24-D12-S (https://www.mouser.cl/ProductDetail/CUI-Inc/PEM2-S24-D12-S?qs=WyjlAZoYn53qVQH5t6xOQA%3D%3D) | DC/DC Converter 24V to +-12V | $9758 | $9758
2 | Melexis | MLX91221KDF-ABF-025-RE | 482-91221KDFABF025RE (https://www.mouser.cl/ProductDetail/Melexis/MLX91221KDF-ABF-025-RE?qs=81r%252BiQLm7BTsp7NzkKjkkA%3D%3D) | Isolation Current Sensor | $6644 | $13288
4 | Bourns | CR0805-FX-1002ELF | 652-CR0805FX-1002ELF (https://www.mouser.cl/ProductDetail/Bourns/CR0805-FX-1002ELF) | SMD Resistor 10k | $109 | $436
2 | KEMET | C1206C561KDGACAUTO | 80-C1206C561KDGAUTO (https://www.mouser.cl/ProductDetail/KEMET/C1206C561KDGACAUTO?qs=MyNHzdoqoQL%252BgGDPneTOTA%3D%3D) | SMD Capacitor 47nF | $972 | $1944
2 | KYOCERA AVX | 0805ZC472KAT2A | 581-0805ZC472KAT2A (https://www.mouser.cl/ProductDetail/KYOCERA-AVX/0805ZC472KAT2A?qs=TtQHvclPtw6GN1UAHPJ7fQ%3D%3D) | SMD Capacitor 4.7nF | $262 | $524
2 | Broadcom / Avago | ACPL-790B-300E | 630-ACPL-790B-300E (https://www.mouser.cl/ProductDetail/Broadcom-Avago/ACPL-790B-300E?qs=jv7ULIbIBgMunF8oouTz%2FA%3D%3D) | Isolation Amplifier | $10424 | $20848
16 | Vishay / Draloric | RCV25122M00FKEGAT | 71-RCV25122M00FKEGAT (https://www.mouser.cl/ProductDetail/Vishay-Draloric/RCV25122M00FKEGAT?qs=DRkmTr78QAQ88fBO7RoMBw%3D%3D) | SMD Resistor 2M | $1519 | $24304
2 | Panasonic | ERJ-UP3F3303V | 667-ERJ-UP3F3303V (https://www.mouser.cl/ProductDetail/Panasonic/ERJ-UP3F3303V?qs=GedFDFLaBXFkDfxcnOlPhw%3D%3D) | SMD Resistor 330k | $284 | $568
2 | ROHM Semiconductor | SFR18EZPJ202 | 755-SFR18EZPJ202 (https://www.mouser.cl/ProductDetail/ROHM-Semiconductor/SFR18EZPJ202?qs=MyNHzdoqoQL%2FgXoFTmyDrQ%3D%3D) | SMD Resistor 2k | $175 | $350
2 | STMicroelectronics | TL074CDT | 511-TL074CDT (https://www.mouser.cl/ProductDetail/STMicroelectronics/TL074CDT?qs=MQjo3npP4sAhBVAvwSx1nw%3D%3D) | Op Amps | $721 | $1442
2 | KYOCERA AVX | SD0805S020S1R0 | 581-SD0805S020S1R0 (https://www.mouser.cl/ProductDetail/KYOCERA-AVX/SD0805S020S1R0?qs=jCA%252BPfw4LHbpkAoSnwrdjw%3D%3D) | Schottky Diode 20V 1A | $404 | $808
1 | Harwin | M20-7820842 | 855-M20-7820842 | Pin socket 5 | $1508 | $1508
4 | Linx Technologies | CONBNC002 | 712-CONBNC002 (https://www.mouser.cl/ProductDetail/Linx-Technologies/CONBNC002?qs=doiCPypUmgFbIbY%252BDq4BiQ%3D%3D) | BNC | $3376 | $13504
1 | Phoenix Contact | 1756993 | 651-1756993 (https://www.mouser.cl/ProductDetail/Phoenix-Contact/1756993?qs=iCzJi%2FIZBF5Zal4EhCc1xA%3D%3D) | Fixed Terminal Blocks (1kV) | $2240 | $2240
1 | CUI Devices | TB002V-500-02BE | 490-TB002V-500-02BE | Fixed Terminal Blocks (24V) | $776 | $776
4 | Samtec | SQT-102-01-F-S | 200-SQT10201FS (https://www.mouser.cl/ProductDetail/Samtec/SQT-102-01-F-S?qs=MUwhXXEU1Qsb9k68Fbb2cw%3D%3D) | Pin socket 2 (gate driver) | $1311 | $5244
1 | KEMET | C2225C104KFRACTU | 80-C2225C104KFR (https://www.mouser.cl/ProductDetail/KEMET/C2225C104KFRACTU?qs=sGAEpiMZZMt7gvpyg0xT8hAhezoVBTlVHdur7LTFsw4%3D) | Ceramic Capacitor 0.1uF | $3278 | $3278
8 | TDK Corporation | CGA2B3X7R1V104K050BB | 810-CGA2B3X7R1V104K (https://www.mouser.cl/ProductDetail/TDK/CGA2B3X7R1V104K050BB?qs=NRhsANhppD%252Bp9zWDEim%2FoA%3D%3D) | Ceramic Capacitor 100nF | $142 | $1136
 |  |  |  |  | Total | $259755

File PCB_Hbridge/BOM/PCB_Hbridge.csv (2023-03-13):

Id | Identificador | Empaquetado | Cantidad | Identificación | Suministrador y ref
1 | U10,U12 | SOIC127P1031X264-16N | 2 | MLX91221KDF-ABF-050-SP
2 | R20,R29 | RESC3216X65N | 2 | 2k
3 | R39,R30,R40,R48,R42,R43,R49,R2,R32,R31,R41 | RESC2012X60N | 11 | 499k
4 | J12 | RHDR5W50P0X200_1X5_1050X240X440P | 1 | M22-7130542
5 | D2,D1 | DIOM1613X100N | 2 | SD0805S020S1R0
6 | C9,C4,C12,C3,C8,C13,C2,C1,C14 | CAPC2012X145N | 9 | 1uF
7 | C20,C18,C17,C15 | CAPC3216X175N | 4 | 47nF
8 | R16,R22,R21,R25,R18,R12,R26,R24,R15,R17,R27,R13,R28,R23,R19,R14 | RESC6332X70N | 16 | 2M
9 | U7,U8 | SOT95P285X140-5N | 2 | AP7366-W5-7
10 | J6 | TB002V50002BE | 1 | TB002V-500-02BE
11 | U5,U6 | CONV_PDSE2-S24-S5-M | 2 | PDSE2-S24-S5-M
12 | U4,U3,U1,U2 | SCT3105KRC14 | 4 | SCT3105KRC14
13 | C28,C24,C26,C22,C27,C25,C29,C23 | CAPC1005X55N | 8 | 100nF
14 | C11,C7,C10 | S103M69Z5UP63K7R | 3 | 0.01uF
15 | R44,R35,R47,R34,R33,R6,R3,R36,R46,R45 | RESC2012X50N | 10 | 120k
16 | H4,H3,H1,H2 | WAT247101E | 4 | WA-T247-101E
17 | R4,R1 | RESC2012X60N | 2 | 56k
18 | C16,C19 | CAPC2012X94N | 2 | 4.7nF
19 | R5 | RESC2012X50N | 1 | 270k
20 | C5,C6 | CAPC3116X180N | 2 | 2.2uF
21 | U11,U13 | DIP762W65P254L980H470Q8N | 2 | ACPL-790B-300E
22 | J2,J3,J4,J1 | SQT-102-01-XX-S | 4 | SQT-102-01-F-S
23 | J5,J7 | 1594460000 | 2 | 1594460000
24 | J8,J10,J11,J9 | CONBNC002 | 4 | CONBNC002
25 | C21 | C2225_DCLINK | 1 | DC-link
26 | R37,R38 | ERJUP3_330k | 2 | 330k
27 | U9 | CONV_PEM2-S24-D12-S | 1 | PEM2-S24-D12-S
28 | U15,U14 | SOIC127P600X175-14N_TL074 | 2 | TL074CDT
29 | L1 | L_Toroid_Horizontal_D69.1mm_P63.20mm_Vishay_TJ9 | 1 | 2.2mH
30 | R9,R7,R50,R11,R10,R8 | RESC2012X60N | 6 | 10k

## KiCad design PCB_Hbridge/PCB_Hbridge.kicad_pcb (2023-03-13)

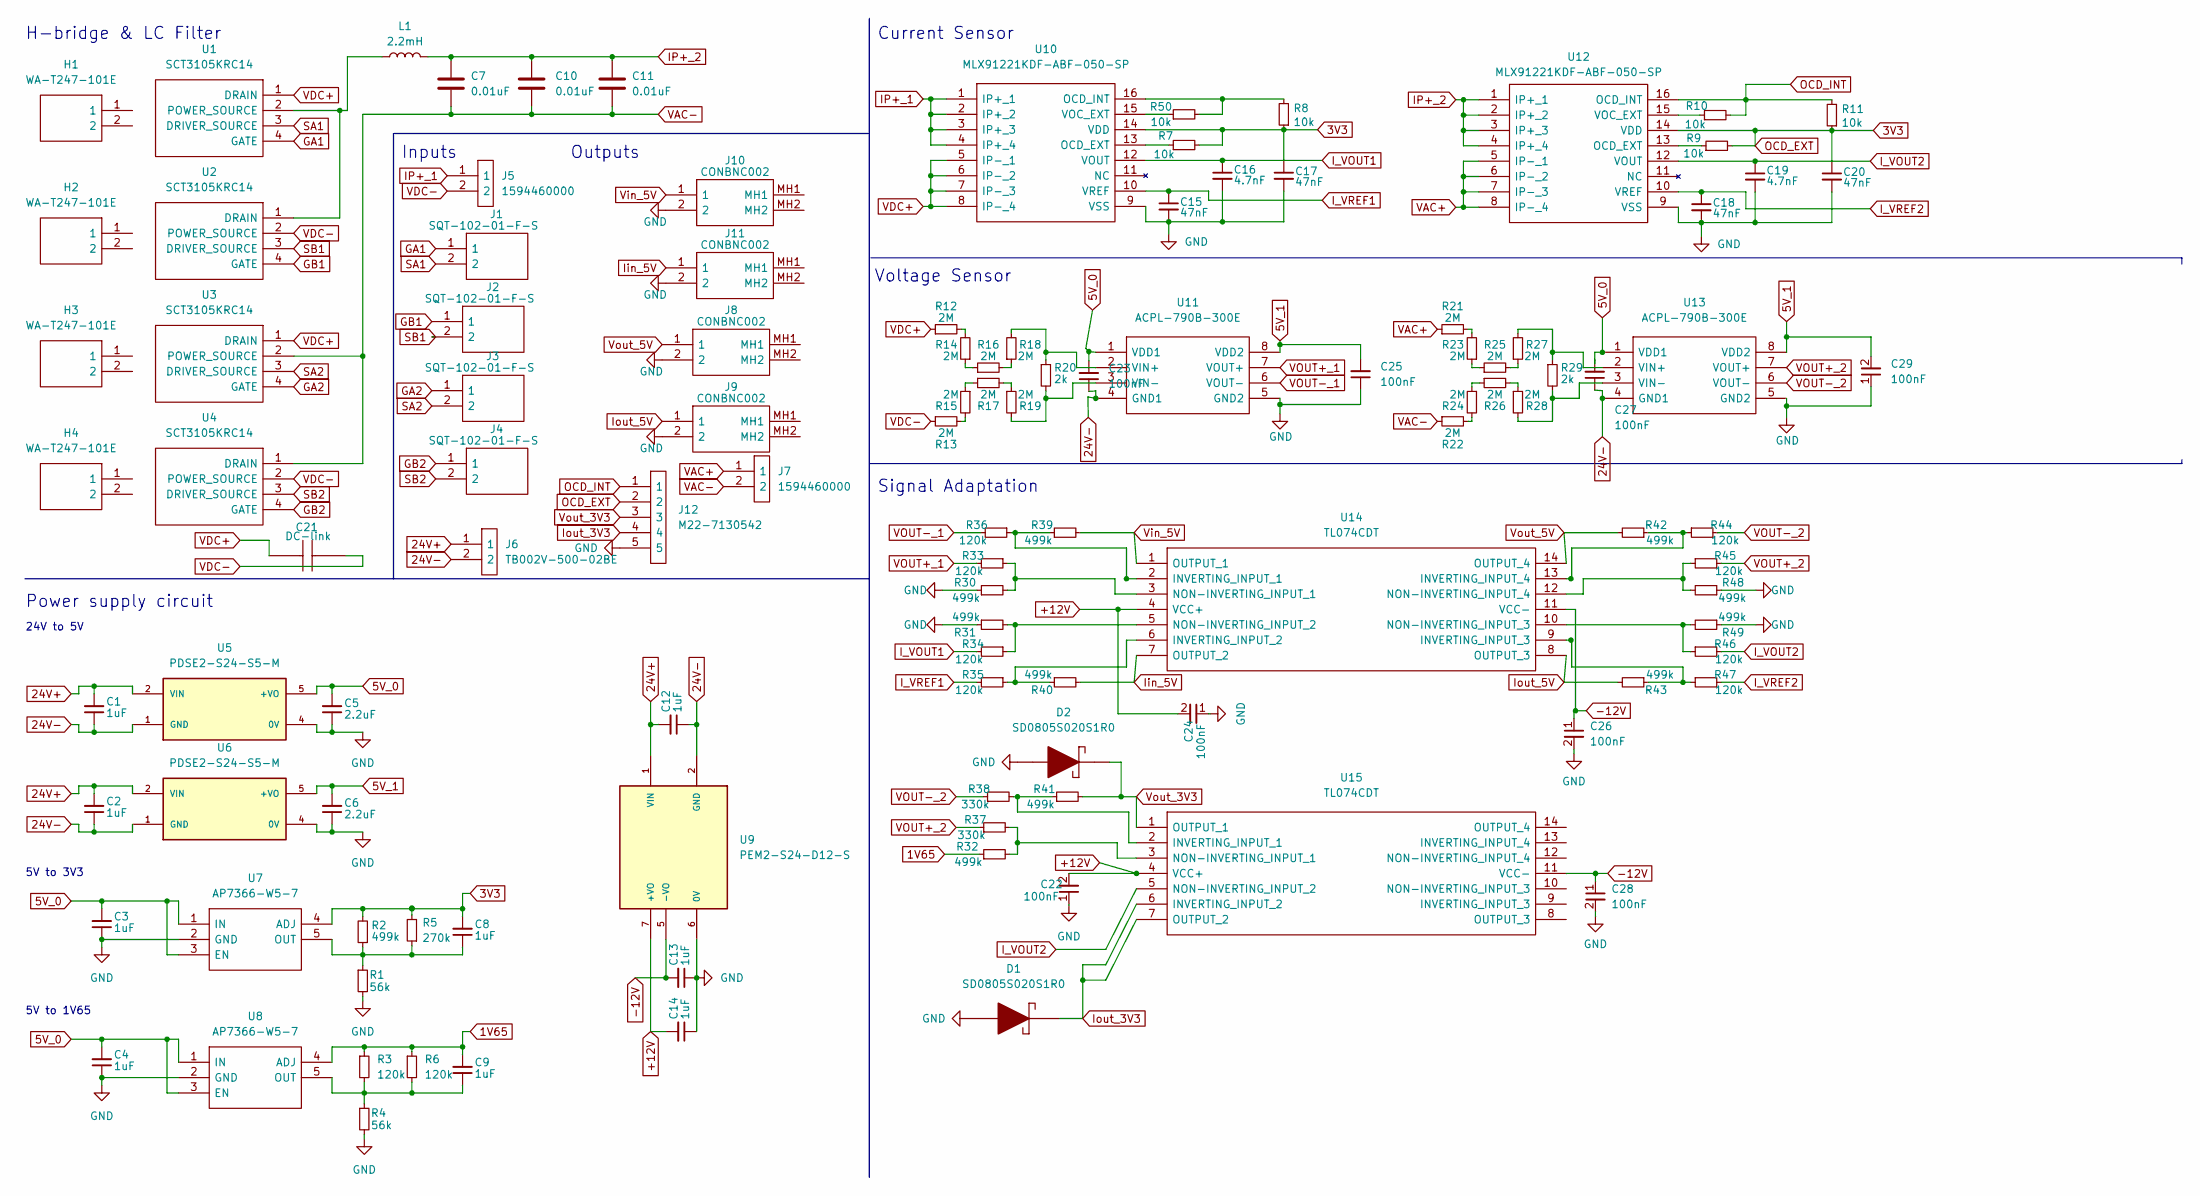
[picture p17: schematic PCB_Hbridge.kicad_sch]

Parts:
C1, C2, C3, C4, C8, C9, C12, C13, C14: 1uF; CAPC2012X145N_01uF; Manufacturer_Part_Number AC0805KFX7R9BB105
C5, C6: 2.2uF; CAPC3116X180N_2_2uF; Mouser Part Number 81-GCM31CR71H225KA5K
C7, C10, C11: 0.01uF; S103M69Z5UP63K7R
C15, C17, C18, C20: 47nF; CAPC3216X175N_47nF; Mouser Part Number 80-C1206C561KDGAUTO
C16, C19: 4.7nF; CAPC2012X94N_4_7nF; Mouser Part Number 581-0805ZC472KAT2A
C21: DC-link; C2225_DCLINK; Mouser Part Number 80-C2225C104KFR
C22, C23, C24, C25, C26, C27, C28, C29: 100nF; CAPC1005X55N_100nF; Mouser Part Number 810-CGA2B3X7R1V104K
D1, D2: SD0805S020S1R0; DIOM1613X100N; Mouser Part Number 581-SD0805S020S1R0
H1, H2, H3, H4: WA-T247-101E; WAT247101E; Mouser Part Number 588-WA-T247-101E
J1, J2, J3, J4: SQT-102-01-F-S; SQT-102-01-XX-S; Mouser Part Number 200-SQT10201FS
J5, J7: 1594460000; Mouser Part Number 470-1594460000
J6: TB002V-500-02BE; TB002V50002BE; Mouser Part Number 490-TB002V-500-02BE
J8, J9, J10, J11: CONBNC002; Mouser Part Number 712-CONBNC002
J12: M22-7130542; RHDR5W50P0X200_1X5_1050X240X440P; Mouser Part Number 855-M22-7130542
L1: 2.2mH; L_Toroid_Horizontal_D69.1mm_P63.20mm_Vishay_TJ9; Manufacturer_Part_Number TJ92UEB222L; Mouser Path Number 70-TJ92UEB222L
R1, R4: 56k; RESC2012X60N_56k; Mouser Part Number 652-CR0805FX-5602ELF
R2, R30, R31, R32, R39, R40, R41, R42, R43, R48, R49: 499k; RESC2012X60N_499k; Mouser Part Number 652-CR0805FX-5602ELF
R3, R6, R33, R34, R35, R36, R44, R45, R46, R47: 120k; RESC2012X50N_120k; Mouser Part Number 652-CR0805FX-5602ELF
R5: 270k; RESC2012X50N_270k; Mouser Part Number 652-CR0805FX-5602ELF
R7, R8, R10, R11, R50: 10k; RESC2012X60N_10k; Mouser Part Number 652-CR0805FX-1002ELF
R9: 10k; RESC2012X60N_10k
R12, R13, R14, R15, R16, R17, R18, R19, R21, R22, R23, R24, R25, R26, R27, R28: 2M; RESC6332X70N_2M; Mouser Part Number 71-RCV25122M00FKEGAT
R20, R29: 2k; RESC3216X65N_2k; Manufacturer_Part_Number SFR18EZPJ202
R37, R38: 330k; ERJUP3_330k; Mouser Part Number 667-ERJ-UP3F3303V
U1, U2, U3, U4: SCT3105KRC14; Mouser Part Number 755-SCT3105KRC14
U5, U6: PDSE2-S24-S5-M; CONV_PDSE2-S24-S5-M; PARTREV 1.0
U7, U8: AP7366-W5-7; SOT95P285X140-5N; Mouser Part Number 621-AP7366-W5-7
U9: PEM2-S24-D12-S; CONV_PEM2-S24-D12-S
U10, U12: MLX91221KDF-ABF-050-SP; SOIC127P1031X264-16N; Manufacturer_Part_Number MLX91221KDF-ABF-050-SP; Mouser Part Number 482-91221KDFABF050SP
U11, U13: ACPL-790B-300E; DIP762W65P254L980H470Q8N; Mouser Part Number 630-ACPL-790B-300E
U14, U15: TL074CDT; SOIC127P600X175-14N_TL074; Mouser Part Number 511-TL074CDT

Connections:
1V65: C9.2, R3.1, R6.1, R32.1, U8.4 (ADJ)
3V3: C8.2, C17.1, C20.1, J12.2, R2.2, R5.2, R7.2, R8.1, R9.2, R11.1, U7.4 (ADJ), U10.14 (VDD), U12.14 (VDD)
5V_0: C3.2, C4.2, C5.2, C23.2, C27.2, U5.5 (+VO), U7.1 (IN), U7.3 (EN), U8.1 (IN), U8.3 (EN), U11.1 (VDD1), U13.1 (VDD1)
5V_1: C6.2, C25.2, C29.2, U6.5 (+VO), U11.8 (VDD2), U13.8 (VDD2)
24V+: C1.2, C2.2, C12.2, J6.1, U5.2 (VIN), U6.2 (VIN), U9.1 (VIN)
24V-: C1.1, C2.1, C12.1, C23.1, C27.1, J6.2, U5.1 (GND), U6.1 (GND), U9.2 (GND), U11.4 (GND1), U13.4 (GND1)
+12V: C14.2, C22.2, C24.2, U9.7 (+VO), U14.4 (VCC+), U15.4 (VCC+)
-12V: C13.2, C26.1, C28.1, U9.5 (-VO), U14.11 (VCC-), U15.11 (VCC-)
GA1: J1.1, U1.4 (GATE)
GA2: J3.1, U3.4 (GATE)
GB1: J2.1, U2.4 (GATE)
GB2: J4.1, U4.4 (GATE)
GND: C3.1, C4.1, C5.1, C6.1, C13.1, C14.1, C15.2, C16.2, C17.2, C18.2, C19.2, C20.2, C22.1, C24.1, C25.1, C26.2, C28.2, C29.1, D1.2, D2.2, J8.2, J9.2, J10.2, J11.2, J12.5, R1.2, R4.2, R30.1, R31.1, R48.1, R49.1, U5.4 (0V), U6.4 (0V), U7.2 (GND), U8.2 (GND), U9.6 (0V), U10.9 (VSS), U11.5 (GND2), U12.9 (VSS), U13.5 (GND2)
IP+_1: J5.1, U10.1 (IP+_1), U10.2 (IP+_2), U10.3 (IP+_3), U10.4 (IP+_4)
IP+_2: C7.1, C10.1, C11.2, L1.2, U12.1 (IP+_1), U12.2 (IP+_2), U12.3 (IP+_3), U12.4 (IP+_4)
I_VOUT1: C16.1, R34.2, U10.12 (VOUT)
I_VOUT2: C19.1, R46.2, U12.12 (VOUT), U15.5 (NON-INVERTING_INPUT_2)
I_VREF1: C15.1, R35.2, U10.10 (VREF)
I_VREF2: C18.1, R47.2, U12.10 (VREF)
Iin_5V: J11.1, R40.2, U14.7 (OUTPUT_2)
Iout_3V3: D1.1, J12.4, U15.6 (INVERTING_INPUT_2), U15.7 (OUTPUT_2)
Iout_5V: J9.1, R43.2, U14.8 (OUTPUT_3)
unnamed: C8.1, R1.1, R2.1, R5.1, U7.5 (OUT)
unnamed: C9.1, R3.2, R4.1, R6.2, U8.5 (OUT)
unnamed: R12.2, R14.2
unnamed: R13.2, R15.2
unnamed: R14.1, R16.1
unnamed: R15.1, R17.1
unnamed: R16.2, R18.1
unnamed: R17.2, R19.1
unnamed: R21.2, R23.2
unnamed: R22.2, R24.2
unnamed: R23.1, R25.1
unnamed: R24.1, R26.1
unnamed: R25.2, R27.1
unnamed: R26.2, R28.1
unnamed: R32.2, R37.2, U15.3 (NON-INVERTING_INPUT_1)
unnamed: R38.2, R41.1, U15.2 (INVERTING_INPUT_1)
unnamed: L1.1, U1.2 (POWER_SOURCE), U2.1 (DRAIN)
unnamed: R7.1, U10.13 (OCD_EXT)
unnamed: R50.1, U10.15 (VOC_EXT)
unnamed: R8.2, R50.2, U10.16 (OCD_INT)
unnamed: R18.2, R20.1, U11.2 (VIN+)
unnamed: R19.2, R20.2, U11.3 (VIN-)
unnamed: R9.1, U12.13 (OCD_EXT)
unnamed: R10.1, U12.15 (VOC_EXT)
unnamed: R27.2, R29.1, U13.2 (VIN+)
unnamed: R28.2, R29.2, U13.3 (VIN-)
unnamed: R36.1, R39.1, U14.2 (INVERTING_INPUT_1)
unnamed: R30.2, R33.1, U14.3 (NON-INVERTING_INPUT_1)
unnamed: R31.2, R34.1, U14.5 (NON-INVERTING_INPUT_2)
unnamed: R35.1, R40.1, U14.6 (INVERTING_INPUT_2)
unnamed: R43.1, R47.1, U14.9 (INVERTING_INPUT_3)
unnamed: R46.1, R49.2, U14.10 (NON-INVERTING_INPUT_3)
unnamed: R45.1, R48.2, U14.12 (NON-INVERTING_INPUT_4)
unnamed: R42.1, R44.1, U14.13 (INVERTING_INPUT_4)
OCD_INT: J12.1, R10.2, R11.2, U12.16 (OCD_INT)
SA1: J1.2, U1.3 (DRIVER_SOURCE)
SA2: J3.2, U3.3 (DRIVER_SOURCE)
SB1: J2.2, U2.3 (DRIVER_SOURCE)
SB2: J4.2, U4.3 (DRIVER_SOURCE)
VAC+: J7.1, R21.1, U12.5 (IP-_1), U12.6 (IP-_2), U12.7 (IP-_3), U12.8 (IP-_4)
VAC-: C7.2, C10.2, C11.1, J7.2, R22.1, U3.2 (POWER_SOURCE), U4.1 (DRAIN)
VDC+: C21.1, R12.1, U1.1 (DRAIN), U3.1 (DRAIN), U10.5 (IP-_1), U10.6 (IP-_2), U10.7 (IP-_3), U10.8 (IP-_4)
VDC-: C21.2, J5.2, R13.1, U2.2 (POWER_SOURCE), U4.2 (POWER_SOURCE)
VOUT+_1: R33.2, U11.7 (VOUT+)
VOUT+_2: R37.1, R45.2, U13.7 (VOUT+)
VOUT-_1: R36.2, U11.6 (VOUT-)
VOUT-_2: R38.1, R44.2, U13.6 (VOUT-)
Vin_5V: J10.1, R39.2, U14.1 (OUTPUT_1)
Vout_3V3: D2.1, J12.3, R41.2, U15.1 (OUTPUT_1)
Vout_5V: J8.1, R42.2, U14.14 (OUTPUT_4)

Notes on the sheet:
Power supply circuit
24V to 5V
Outputs
Current Sensor
5V to 1V65
Signal Adaptation
5V to 3V3
Inputs
H-bridge & LC Filter
Voltage Sensor

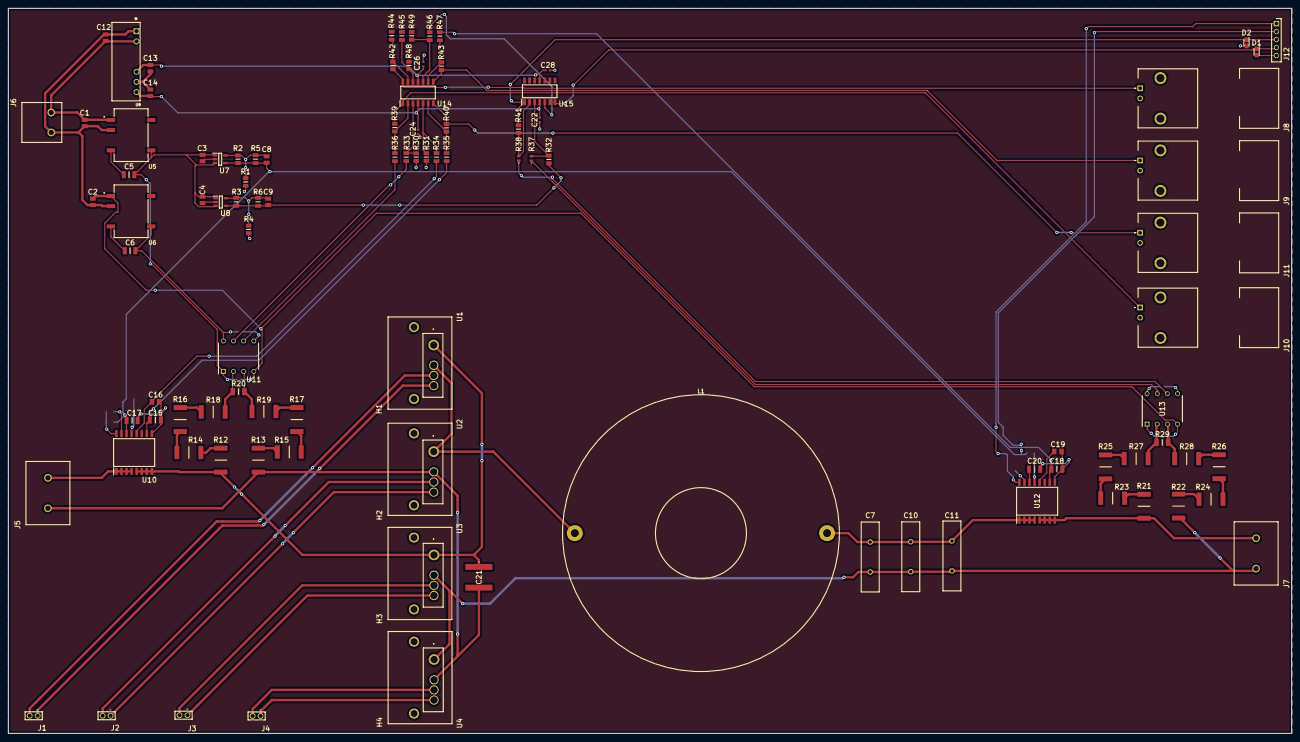
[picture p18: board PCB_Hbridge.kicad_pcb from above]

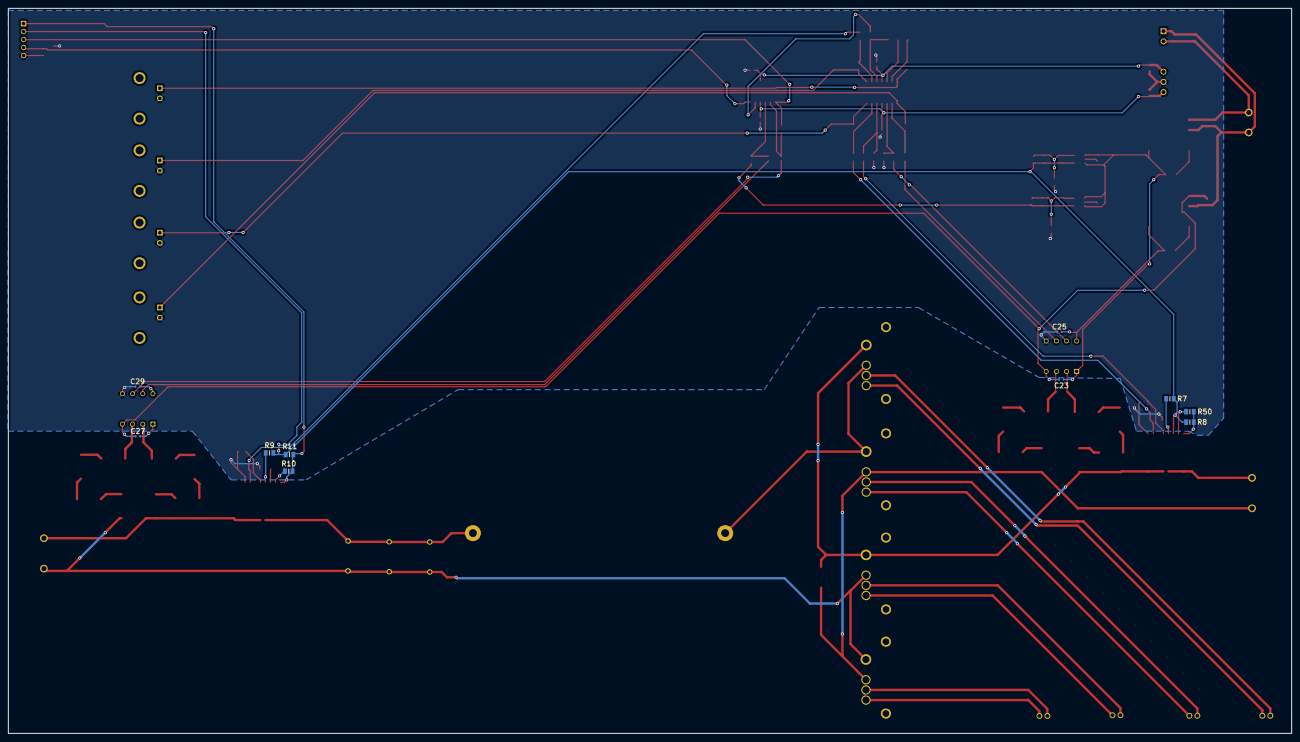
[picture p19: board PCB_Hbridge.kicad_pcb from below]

Board: 2 copper layers, 321.4 x 181.6 mm, 113 parts (10 on the bottom side), 72 nets.

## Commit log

2023-01-23 first time
    [prueba_1.kicad_pcb, prueba_1.kicad_sch]
2023-02-01 Presupuesto estimado
    [BOM_v1.xlsx]
2023-03-13 Add files via upload
    Documentación del desarrollo de la PCB.
